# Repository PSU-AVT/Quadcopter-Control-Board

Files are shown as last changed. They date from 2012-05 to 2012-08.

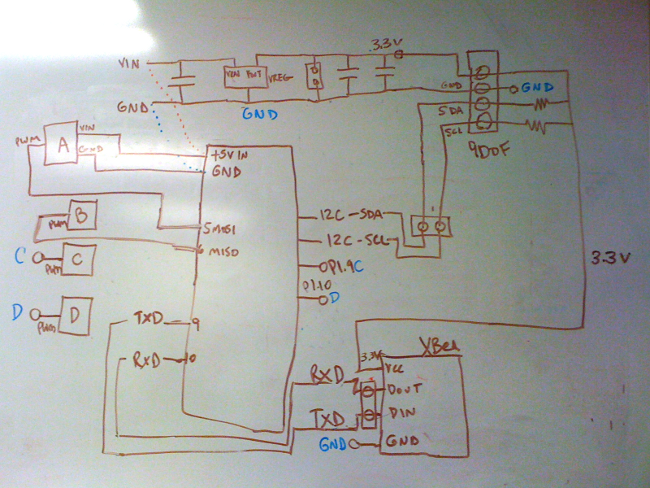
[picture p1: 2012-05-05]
v1-controlboard-schematic.png

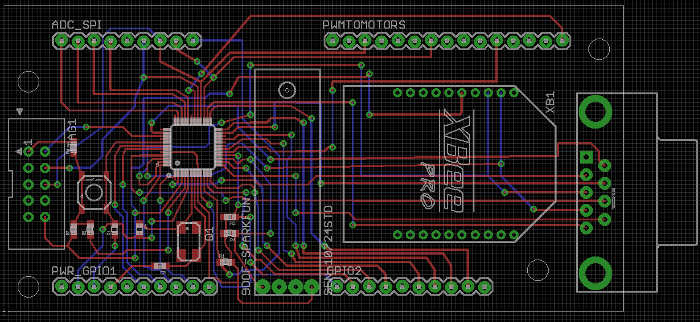
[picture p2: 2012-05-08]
v2-layout-firstreview.png

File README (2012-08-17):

Autonomous Vehicles Team
Quadcopter Control Board

v1 (protobard)

v2 (first pcb) built and found to have no functioning power layer, and the TxD/RxD lines were swapped between the processor and the FTDI serial out. The XBee serial worked correctly.  

v3 (current pcb) modified the clock traces, added a mini-USB connector and 5V-3.3V regulator, fixed the RxD/TxD oops, and hopefully repaired the power plane issue. Gerbers have been submitted but won't be tested until early October due to vacations. 

Built collaboratively by Jenner Hanni (wicker), Camille Huffman Day (squidpie), and Greg Haynes (greghaynes). Huge thanks to Andrew Greenberg, Bart Massey, Chris, and Tim from the Portland State Aerospace Society.

These files use the MIT License.

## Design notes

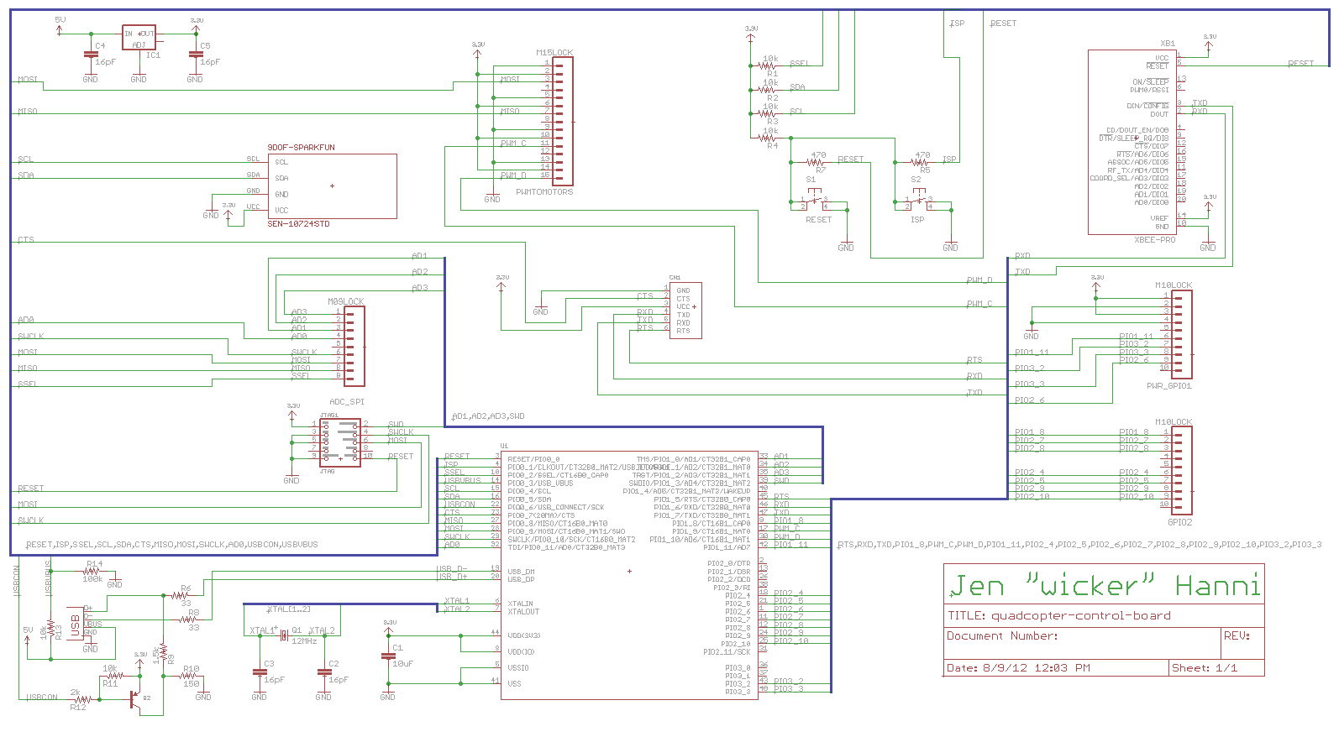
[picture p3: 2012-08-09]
v3-schema-final.png

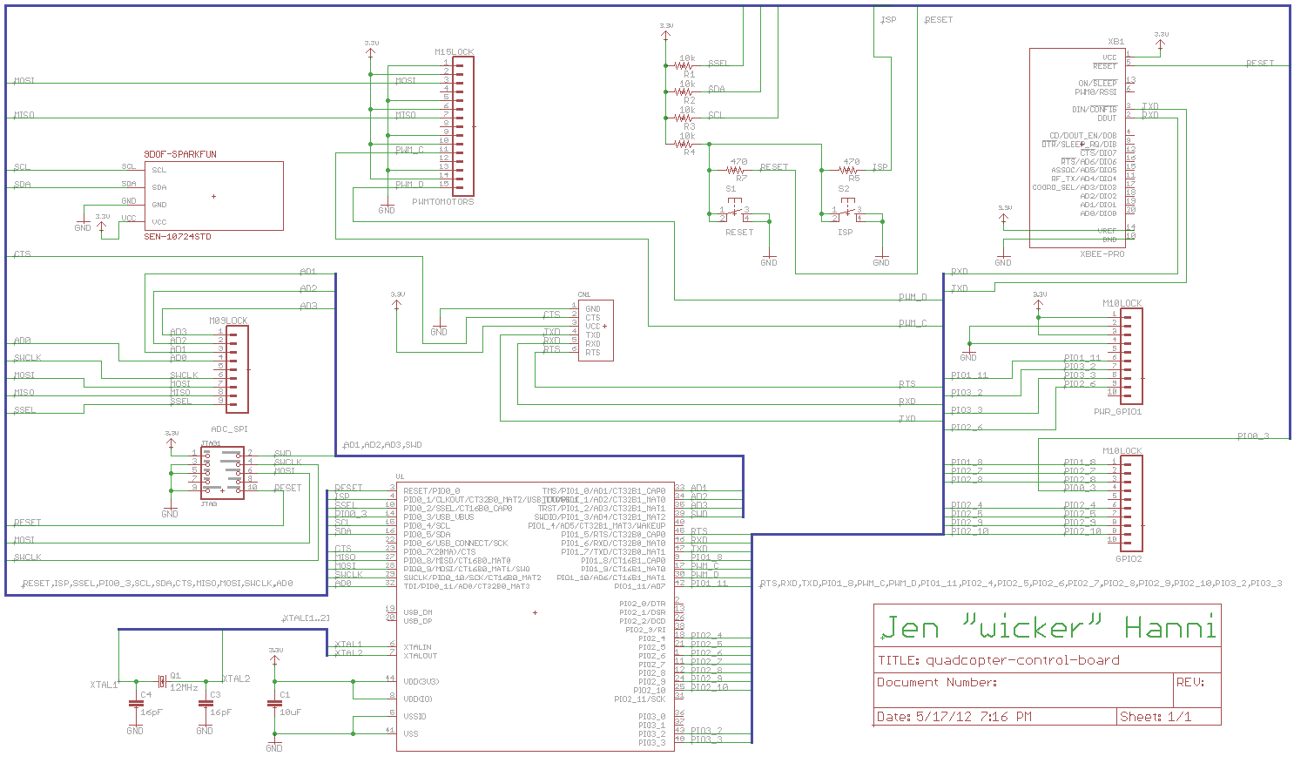
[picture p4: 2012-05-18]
v2-schema-final.png

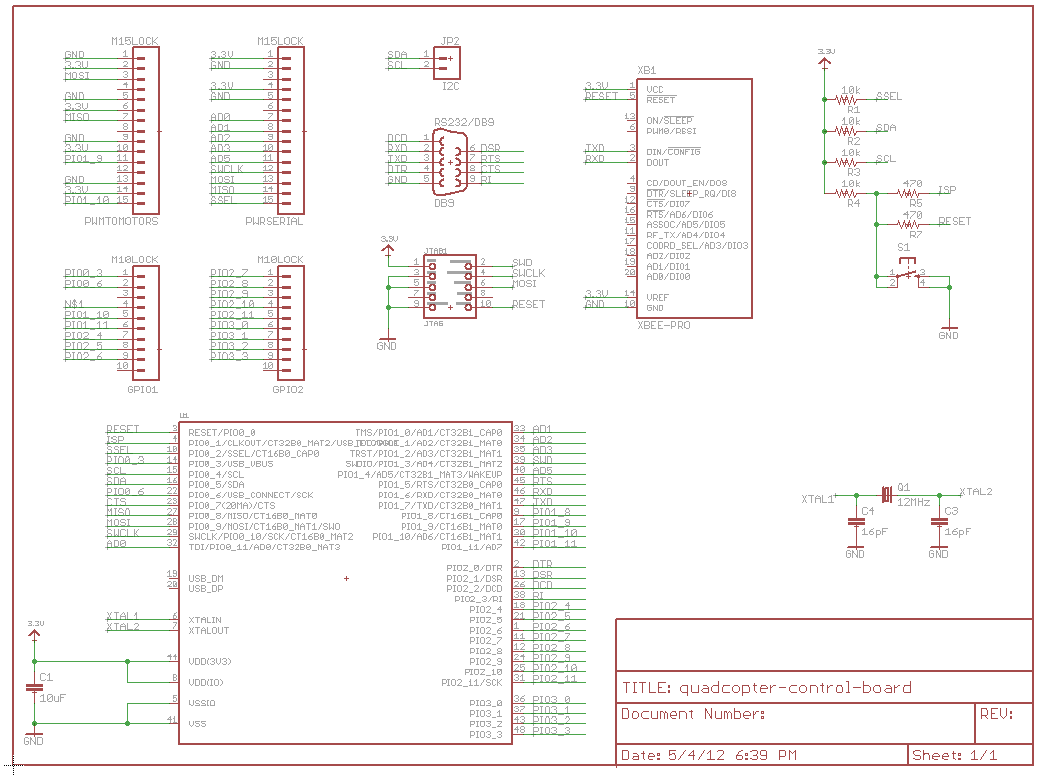
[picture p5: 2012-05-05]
v2-schema-firstreview.png

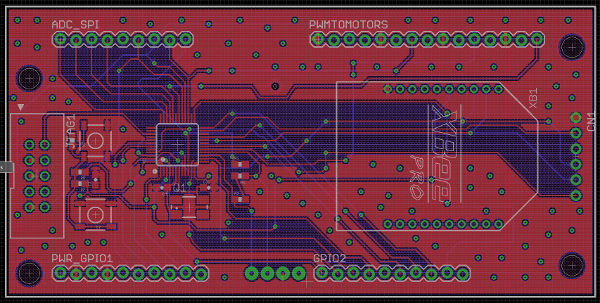
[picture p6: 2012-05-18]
v2-layout-final.png

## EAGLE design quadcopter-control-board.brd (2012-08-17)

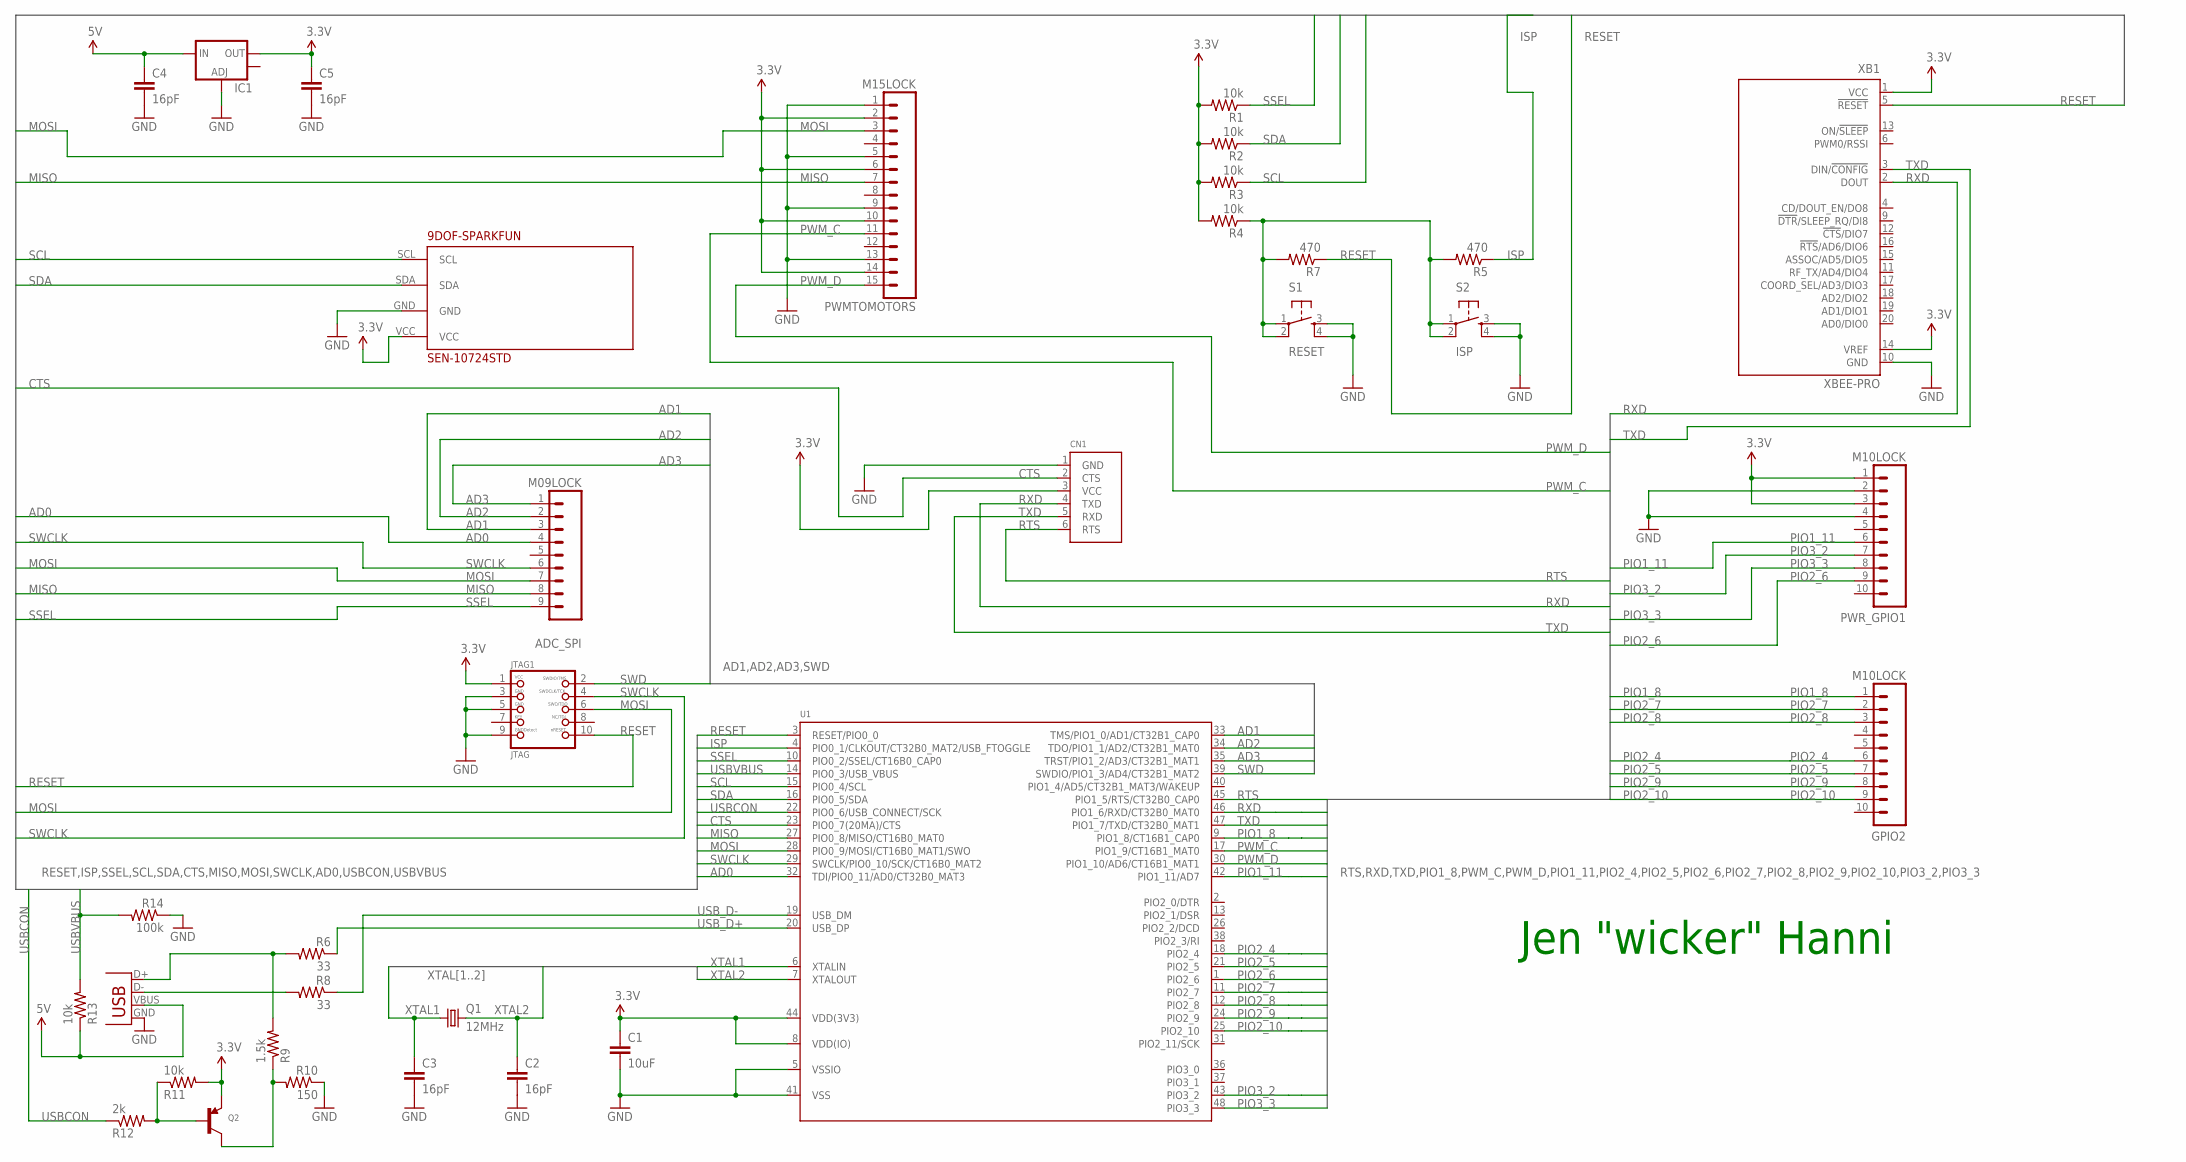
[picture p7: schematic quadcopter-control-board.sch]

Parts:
9DOF-SPARKFUN: SEN-10724STD; SPARKFUN-9DOF
ADC_SPI: M09LOCK; 1X09_LOCK
C1: 10uF; 0603-CAP
C2, C3, C4, C5: 16pF; 0603-CAP
CN1: FTDIUSBCABLE; 1X06_ROUND
GPIO2: M10LOCK; 1X10_LOCK
IC1: V_REG_LM1117SOT223; SOT223
JTAG1: JTAG; CORTEXM3_SWD10_MOLEX
PWMTOMOTORS: M15LOCK; 1X15_LOCK
PWR_GPIO1: M10LOCK; 1X10_LOCK
Q1: 12MHz; CTS406
Q2: TRANSISTOR_PNPSOT23-REFLOW; SOT23-R
R1, R2, R3, R4, R11, R13: 10k; 0603-RES
R5, R7: 470; 0603-RES
R6, R8: 33; 0603-RES
R9: 1.5k; 0603-RES
R10: 150; 0603-RES
R12: 2k; 0603-RES
R14: 100k; 0603-RES
S1: RESET; TACTILE_SWITCH_SMD
S2: ISP; TACTILE_SWITCH_SMD
U1: LPC1343_QFP; LQFP48
X1: USB-SMD-NS; USB-MINIB-NOSTOP
XB1: XBEE-PRO

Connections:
3.3V: 9DOF-SPARKFUN.VCC, C1.1, C5.1, CN1.3 (VCC), IC1.2 (OUT), JTAG1.1, PWMTOMOTORS.2, PWMTOMOTORS.6, PWMTOMOTORS.10, PWMTOMOTORS.14, PWR_GPIO1.1, PWR_GPIO1.3, Q2.2 (E), R1.2, R2.2, R3.2, R4.2, R11.2, U1.8 (VDD(IO)), U1.44 (VDD(3V3)), XB1.1 (VCC), XB1.14 (VREF)
5V: C4.1, IC1.3 (IN), R13.1, X1.VBUS
AD0: ADC_SPI.4, U1.32 (TDI/PIO0_11/AD0/CT32B0_MAT3)
AD1: ADC_SPI.3, U1.33 (TMS/PIO1_0/AD1/CT32B1_CAP0)
AD2: ADC_SPI.2, U1.34 (TDO/PIO1_1/AD2/CT32B1_MAT0)
AD3: ADC_SPI.1, U1.35 (TRST/PIO1_2/AD3/CT32B1_MAT1)
CTS: CN1.2 (CTS), U1.23 (PIO0_7(20MA)/CTS)
GND: 9DOF-SPARKFUN.GND, C1.2, C2.2, C3.2, C4.2, C5.2, CN1.1 (GND), IC1.1 (ADJ), JTAG1.3, JTAG1.5, JTAG1.9, PWMTOMOTORS.1, PWMTOMOTORS.5, PWMTOMOTORS.9, PWMTOMOTORS.13, PWR_GPIO1.2, PWR_GPIO1.4, R10.1, R14.1, S1.3, S1.4, S2.3, S2.4, U1.5 (VSSIO), U1.41 (VSS), X1.GND, XB1.10 (GND)
ISP: R5.1, U1.4 (PIO0_1/CLKOUT/CT32B0_MAT2/USB_FTOGGLE)
MISO: ADC_SPI.8, PWMTOMOTORS.7, U1.27 (PIO0_8/MISO/CT16B0_MAT0)
MOSI: ADC_SPI.7, JTAG1.6, PWMTOMOTORS.3, U1.28 (PIO0_9/MOSI/CT16B0_MAT1/SWO)
unnamed: R6.2, R9.2, X1.D+
unnamed: R8.2, X1.D-
unnamed: Q2.3 (C), R9.1, R10.2
unnamed: Q2.1 (B), R11.1, R12.2
unnamed: R4.1, R5.2, R7.2, S1.1, S1.2, S2.1, S2.2
PIO1_8: GPIO2.1, U1.9 (PIO1_8/CT16B1_CAP0)
PIO1_11: PWR_GPIO1.6, U1.42 (PIO1_11/AD7)
PIO2_4: GPIO2.6, U1.18 (PIO2_4)
PIO2_5: GPIO2.7, U1.21 (PIO2_5)
PIO2_6: PWR_GPIO1.9, U1.1 (PIO2_6)
PIO2_7: GPIO2.2, U1.11 (PIO2_7)
PIO2_8: GPIO2.3, U1.12 (PIO2_8)
PIO2_9: GPIO2.8, U1.24 (PIO2_9)
PIO2_10: GPIO2.9, U1.25 (PIO2_10)
PIO3_2: PWR_GPIO1.7, U1.43 (PIO3_2)
PIO3_3: PWR_GPIO1.8, U1.48 (PIO3_3)
PWM_C: PWMTOMOTORS.11, U1.17 (PIO1_9/CT16B1_MAT0)
PWM_D: PWMTOMOTORS.15, U1.30 (PIO1_10/AD6/CT16B1_MAT1)
RESET: JTAG1.10, R7.1, U1.3 (RESET/PIO0_0), XB1.5 (!RESET)
RTS: CN1.6 (RTS), U1.45 (PIO1_5/RTS/CT32B0_CAP0)
RXD: CN1.4 (TXD), U1.46 (PIO1_6/RXD/CT32B0_MAT0), XB1.2 (DOUT)
SCL: 9DOF-SPARKFUN.SCL, R3.1, U1.15 (PIO0_4/SCL)
SDA: 9DOF-SPARKFUN.SDA, R2.1, U1.16 (PIO0_5/SDA)
SSEL: ADC_SPI.9, R1.1, U1.10 (PIO0_2/SSEL/CT16B0_CAP0)
SWCLK: ADC_SPI.6, JTAG1.4, U1.29 (SWCLK/PIO0_10/SCK/CT16B0_MAT2)
SWD: JTAG1.2, U1.39 (SWDIO/PIO1_3/AD4/CT32B1_MAT2)
TXD: CN1.5 (RXD), U1.47 (PIO1_7/TXD/CT32B0_MAT1), XB1.3 (DIN/!CONFIG)
USBCON: R12.1, U1.22 (PIO0_6/USB_CONNECT/SCK)
USBVBUS: R13.2, R14.2, U1.14 (PIO0_3/USB_VBUS)
USB_D+: R6.1, U1.20 (USB_DP)
USB_D-: R8.1, U1.19 (USB_DM)
XTAL1: C3.1, Q1.1, U1.6 (XTALIN)
XTAL2: C2.1, Q1.3 (2), U1.7 (XTALOUT)

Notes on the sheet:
Jen "wicker" Hanni

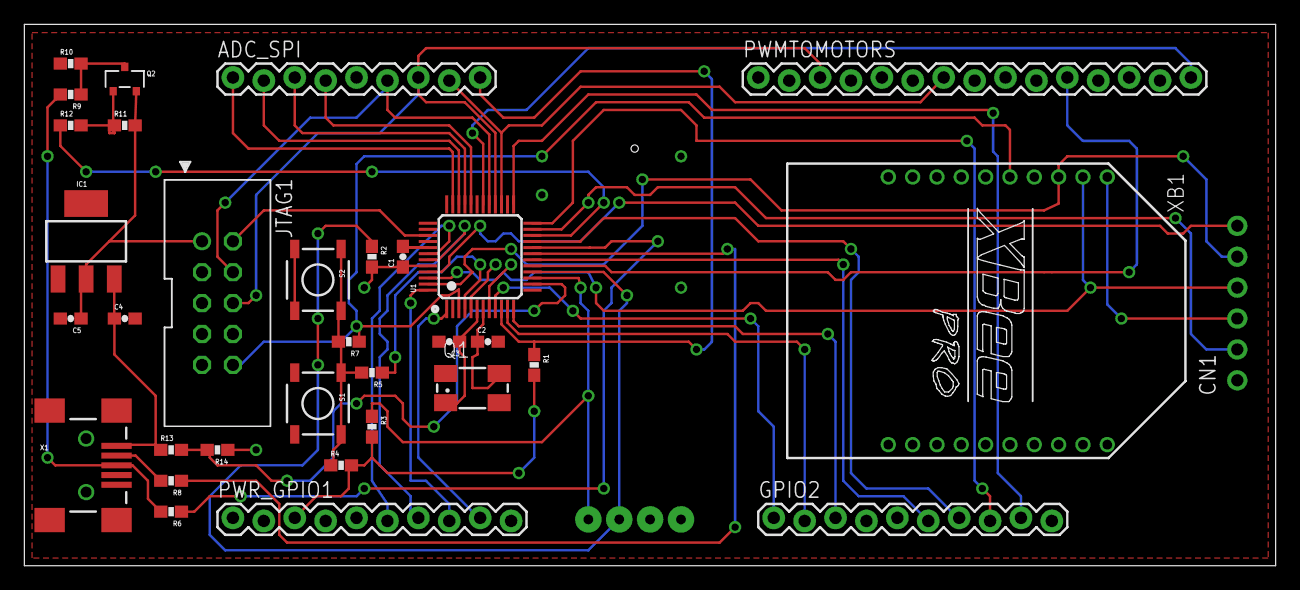
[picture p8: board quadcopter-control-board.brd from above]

Board: 4 copper layers, 102.8 x 44.5 mm, 34 parts (0 on the bottom side), 44 nets.

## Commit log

2012-03-15 First commit.
    [quadcopter-control-board.sch]
2012-05-01 Laid it out from scratch, everything but 9DOF and serial/pwm headers is in the schematic.
    [quadcopter-control-board.sch]
2012-05-04 Removed USB as per design review.
    [quadcopter-control-board.sch]
2012-05-05 Added 2x5 standard 0.05" SWD connector.
    [quadcopter-control-board.sch]
2012-05-05 All serial, GPIO, power pins on nets. Layout in schematic looks good. No error check yet.
    [quadcopter-control-board.sch]
2012-05-05 All errors handled, nets verified. Ready for layout.
    [quadcopter-control-board.sch]
2012-05-05 I have no idea what I'm doing with this layout process.
    [quadcopter-control-board.brd, quadcopter-control-board.sch]
2012-05-05 Made 9DOF footprint, added it. Started board layout.
    [quadcopter-control-board.brd, quadcopter-control-board.sch]
2012-05-05 PWM, JTAG, 9DOF mostly laid out.
    [quadcopter-control-board.brd]
2012-05-06 Reworked the header pins to make layout more compact.
    [quadcopter-control-board.sch]
2012-05-06 Better layout, reworked headers. Half-laid out.
    [quadcopter-control-board.brd, quadcopter-control-board.sch]
2012-05-06 All traces linked! Needs clearance, overlap issues resolved.
    [quadcopter-control-board.brd]
2012-05-08 Board layout finished, ERC good. DRC throwing layer setup errors for GND/VCC.
    [quadcopter-control-board.brd, quadcopter-control-board.sch]
2012-05-08 Image of PCB layout, needs design review.
2012-05-15 Needs buses.
    [quadcopter-control-board.sch]
2012-05-15 Add ground, 3.3V layers with polygons. Requires ripup; and start over.
    [quadcopter-control-board.brd]
2012-05-15 Replaced DB9 with FTDI. Moved crystal caps closer to microprocessor. Vias 0.013 drill size. Added top ground fill. Isolation distance 0.05 inch.
    [quadcopter-control-board.brd, quadcopter-control-board.sch]
2012-05-17 Add XTAL bus. Needs rest of buses, move components, enlarge area.
    [quadcopter-control-board.sch]
2012-05-17 Reconnect all lines, place ground vias. Ready to ship to Mr PCB Man.
    [quadcopter-control-board.brd]
2012-05-18 Place buses on SCH. Board and schematic consistent. Pass ERC and DRC. Ready to fab.
    [quadcopter-control-board.brd, quadcopter-control-board.sch]
2012-06-05 Lay out board to fix ground plane issues.
    [quadcopter-control-board.sch]
2012-06-21 Modify oscillator layout so XTAL1 and XTAL2 are symmetrical, closer, more direct.
    [quadcopter-control-board.brd]
2012-07-04 Photo of top layer of newly fabricated board.
2012-08-09 Fix RxD,TxD. Add 5 to 3.3V reg. Add mini USB. Passes ERC.
    [quadcopter-control-board.sch]
2012-08-09 Fix RxD and TxD. Add 5 to 3.3V regulator. Add mini USB. Passes ERC.
    [quadcopter-control-board.sch]
2012-08-09 Position new main elements, clean up areas and ripup old wires.
    [quadcopter-control-board.brd]
2012-08-17 Quadcopter Board v2 is ready to go.
    [quadcopter-control-board.sch]
2012-08-17 Adding v3.
    [quadcopter-control-board.brd, quadcopter-control-board.sch]

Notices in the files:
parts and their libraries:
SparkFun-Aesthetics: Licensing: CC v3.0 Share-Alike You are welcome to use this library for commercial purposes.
